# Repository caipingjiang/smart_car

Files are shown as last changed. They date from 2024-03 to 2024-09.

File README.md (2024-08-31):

# 备战日记及感悟
## 十九届智能视觉备战
### 2024/4/10
昨晚偶然间又看了木哥的备战“日记”， 感受很多，颇受启发。感受到有许多值得咱们学习的地方：
- 每个一段时间就反思总结， 回顾近段时间做了什么，明晰下一阶段应该做什么
- 提高效率，有时不要太意气用事，多点理性
- 学习永无止境，热爱就是动力，学习英语即使如此，不必感到烦恼，把它权当你技术学习上的工具，每天坚持
  当然还有许多值得学习借鉴的地方，哈哈，就这么简单写点吧，以后这可以作为我们交流、分享讨论的地方，鼓励大家也来多写写心得体会，bye

### 2024/4/11
目前阶段现状：
1. PCB焊接未搞定(如果板子没问题，尽量在下周结束之前完成-21号)
2. 卡片数据集还有许多类别未拍，可以每天有空就拍一类，轮流拍，完成每日任务任务，不要过于依赖学弟， 导致拍的效率很低？（江老师说得对，压榨学弟不如压榨自己）
3. 车硬件总体调试（尽快要完成了，不能再拖， 周末之前完成）
4. 元素识别稳定性加强，以及在元素部分赛道的运动控制还没完成
5. OpenArt 目标检测以及串口传输数据（如何确保信息的准确性，考虑滤掉一些信息）

故下周主要任务就是4，5，争取让车车先跑起来，模型的准确性先不提
这周拍完数据集，打完标签开始炼丹，不能再拖了

### 2024/4/11
今日工作，像机器人一样拍照，莫得感情，明天继续，拍完四类，难受。
### 2024/4/14
受到木哥指点，认真检查驱动板的焊接，发现普遍存在的虚焊问题，焊了一天板子成功修好以前失败的三块驱动板，焊接技术进阶
数据集拍完，驱动板完成。

### 2024/4/16
下阶段任务 完成二代机械结构，框架加宽，机械臂优化，这次依然使用3d打印，后期优化替换
           探索炼丹技巧
           定下目标检测及分类识别的思路，测试openart可以运行两个模型，但可能是框选不标准导致识别率极低。目标检测重拍，如何拍？
           争取下周之前焊好主板，将车车以前学长的硬件结构替换为自己的，完成硬件任务
           最最最最重要！！！！！！背单词，考四级！

### 2024/5/1
   五一九天假？直接完赛？
   目前阶段现状：主板焊完测试完成，硬件结构以全部替换，机械结构完成，硬件任务完成
                炼丹一直是废丹，继续探索炼丹技巧
                控制代码不断完善，十字运行状态良好，下一步与openart结合进行控制，捡卡片的思路？
                openart分类识别时如何准确的框选出图片？
                调参这种事现阶段还是不要浪费太多时间，还没到死磕的时候目前就是调差不多能用就行吧
       九天的假期相比于之前零碎时间效率还是很高的，这段时间争取完成大部分任务，这段时间也是通宵了两天，（江老师是真的狠人，
     动不动就要调一晚上，相比江老师做的任务量，非常的自愧不如，比起江老师感觉自己有点摆，无比惭愧。注：后面打的都是身体战，如果现在不好好休息，
     后面是绝对撑不住的，江老师保重身体啊！）希望可以利用这次假期完赛吧。（献祭一个江老师）

### 2024/5/2

### 2024/5/3
现在是早上五点，差不多熬了一晚上，现在倒是挺精神的😂，张老师说的没错：后面打的都是身体战！回过头来看看这两三天的调车时光，确实，这就是差距的，一个代码写出来总会遇到各种bug,总是要调试很多次取找出bug所在，每次烧录完程序自信满满地以为这次绝对能行，可最后往往以打脸结束。代码框架先在脑海中初具雏形，到反复调试，找bug, 能运行，考量优化，其实我觉得有很大一部分时间浪费在找bug上。有时觉得自己效率太低，调了半天车，没什么进展，往往内耗自己的情绪；有时做一个事情，半路里觉得“有必要”去先完成另外一件事情，另一件事情做了回儿，觉得另另一件事应该先完成，哈哈，这就是顾此失彼啊，没有把握重点。每天先明晰第一优先级要做的是什么，如果被其他打断，有必要去做那么不是很有必要的事吗？往往是做这做那，就忘了根本的目的。希望以后引以为戒

前段时间张老师也是花了很多时间完成了驱动板和主板的焊接，也算是取得了突破性进展，我要称之为“大交汉武帝”，这几天调车哥们也是一起肝啊，也是辛苦了张老师咧
五一假期已过半，还有几天时光，分析一下下一阶段的工作：
- 练得一手好单，张老师也是练了很多丹了，但效果不是那么令人满意，下一阶段和张老师探讨一下，请教学长
- 该上openart了，先挑卡片矫正，目标检测若效果还行可以加上目标检测看看矫正效果
- 组织一下几个摄像头与核心板的通讯，分析一下总体通讯（小车控制）逻辑
- 数字字母的分类数据集应该也可以拍一拍了，这个效果应该很好
- 可以先拿个MCX Vision玩玩，了解以下怎么使用？

### 2024/5/6
 ！！！！丹成！！！！！
 也是和兄弟们又通宵一天，这次也是有两个学弟的陪伴，学弟的效率也是很高的，一晚上就打完了几千张照片的标签，不知道这算不算压迫学弟😝。
 也是在今天早上终于成神丹，过程也是有点难崩，我可能已经错过了好几次成神丹的机会了，前面无数次效果令人不满意的废丹其实是因为验证错误的问题，
 他们很有可能是神丹的😭，具体原因是逐飞给的分类识别的脚本 img.copy(r.rect()) 的使用错误，它并没有copy出感兴趣区域，而是使用的整个图像，
 这也是在使用目标检测后框出不理想框反而判断更精准而发现，因而出现了种种我们认为不理想的丹，将它改为 img1 = img.copy(1,1, r.rect())  
 就可以了，从中的感悟也是颇深😊。
  放假的这段时间虽然没有完赛但效率也是非常高的，也是和江老师通宵了四五天，现在生物钟都混乱了

- 完成炼丹任务
- 目标检测训练完成，90度分类目标检测良好，虽然可能框的不太准确，但好在丹硬，识别率还是非常高的，130度目标检测效果不太好，会出现近处标不出的问题，后面可能需要重练
- 数字字母的分类识别虽然只练了150多轮，准确率也是高的离谱
- 今天还发现调整openart的亮度也就是曝光时间会影响帧率，在降低曝光时间后帧率提高显著，所以补光灯变成了非常有必要了
- 目前来说任务就只剩和openart结合进行控制了，至于其他的暂且把他们归为优化项（换五分类？换碳板？），目前保证先完赛吧
- 自从调车后也是有点厌学，四级已经一个月没看了😭😭😭，感觉需要找点时间学学四级😔😔

### 2024/5/22
近两周进度推进缓慢，有些停滞
目前mcx已能用于目标检测，部署到实际的行车环境，今晚简单调了下，还有些小问题。
- 弯道可能识别不到卡片，可能是参考点的选择不太合理或者距离计算公式得优化
- 有时会误识别，导致转错方向，why?
- 仓舵机仍是一大问题，时不时还会发癫痫，今晚换了线，明天再试试会不会有问题
- bug:有时转向后会倒着走？
- 主板电源电路的问题，现在先放放？？？？？

下一阶段（6/1之前）：
- 把上面提到的问题，解决
- 把分类加上去，实现与仓配合
- 十字环岛逻辑控制完成
- 放置卡片

加油啊xdm，完成上面的内容也基本完赛了，**提高效率与执行力，不要再拖了**
<u>时间过得很快!!!</u>
<u>时间过得很快!!!</u>
<u>时间过得很快!!!</u>
早日完赛！⛽

### 2024/6/5
!!!!!完赛!!!!!
计划的完赛日期一拖再拖，终于还是完赛了（虽然坡道和障碍还没写😁），完赛情况比预期要好，虽然存在一些问题，但还是比较丝滑。
- 仓抖的问题解决，和预期的一样是因为杜邦线接触不良，也可能是主板硬件的毛病（当时少几类电阻就直接拿差不多阻值的代替了，有点随便😝）在换了线和焊了一块新主板之后就稳得很
- mcx目标检测的问题解决，之前的种种问题完全是因为屏幕太小没有显示整张图像，造成了很多假想的问题，换了块大屏幕之后问题就自然消失了，所以说在调车的时候最忌讳盲调，一定要有人机交互的端口，屏幕或者无线串口。
- openart的卡死问题解决，这个问题也是困扰了我很多天，每天都非常煎熬，以为是内存的问题，因为毕竟运行了三个模型，为此还爆金币又买了一个art(当时舵机也是，一开始以为是坏了，又买了两个舵机，太贵了😭，但是无所谓了，有备着的总是好的，就算是给学弟的积累财富吧，毕竟我们也是传承了木哥当年的车车和大部分元件，希望能传承下去吧），也是今天晚上试车时偶然发现，我们的openart程序中的roi会超出边界，具体原因是因为目标检测框出来的roi会整体偏左，所以在使用roi时进行了手动调整，比如x1 = int((x1-0,1)*img.width())，这时候问题就来了，假如手动调整过后x1,小于零，那么roi显然已经超出了图像范围，所以可以对此加以筛选，if x1<0:  x1=0，就可解决。
- 目前的最急需解决的问题就是放卡片和捡卡片不能一次完成，主要问题是矫正的位置不精确和电磁铁的问题，当然有可能是卡片本身的问题，当时粗制烂造的卡片也是深受其害

-所以下阶段的任务-

- 把避障和坡道的代码写完，坡道可以选择直接不走或加辅助轮冲过去
- 解决放卡片和捡卡片问题，试一试换一个电磁铁，优化一下机械臂路径，优化卡片矫正的算法
- 试车调车，每天都跑一跑车真的有用，每次跑几乎都能发现问题，还有一下隐藏的不容易出现的问题，边试边调一直是我们调车的最佳方案

### 2024/6/5
从前几天开始已经陆续完赛了，昨天又熬了一夜，解决了很多的bug,对控制进行了优化，运行起来丝滑了许多，目前识别和分类的正确率也得到保证了，到目前为止可以说已经基本完赛，若不提完赛用时的话运行起来还算比较稳定，有一定鲁棒性。虽然比预期的完赛日期晚了几天，但也总算完赛了，先庆祝一下🥳🎉

回归之前的问题，这里简单做下总结：
1.卡片的距离计算公式似乎不用太精确，以前以为mcx的前瞻因该很远，故需判断卡片的距离，但目前我们的mcx的前瞻调的较低，画面中只要有卡片，说明就已经不远了，所以这里简单的用像素点之间的距离来代表两者之间的距离，效果也是可以的，所以啊空想不如实际去动手试一下
2.仓舵机的问题之前一直萦绕了我们很久，也换过舵机，买过新舵机，仍然不行，最后发现是**杜邦线接口松动**的问题，只能说"踏破铁鞋无觅处，得来全不费工夫"，现在仓转的很标准，回想之前的转角，一会就差个5度10度，不然就疯狂抖动，现在心情舒畅了
3.转向后倒着走因为识别到了车底盘，同时之前的位置矫正如果坐标不刷新就会一直保持上一状态，导致可能走出赛道，现已改进

下一阶段就是不断测试，不断找潜在的bug,同时进行优化，提高稳定性与完赛速度，目前有以下几点：
0.首先把剩下的坡道和障碍物解决
1.用于分类的目标检测框照片可能还是稍有问题：可以考虑重新框，框得越准自然分类的正确率就会越高
2.加上错误修复，**提高整体的容错性**，比如即使在十字逻辑发生了错乱也不影响在环岛进行操作
3.之前的边界矫正稍微还有点问题，看看能优化进一步提高鲁棒性
4.去掉不必要的延时，在保证卡片识别正确率的基础上加快运行速度，看看能不能到**5min**以内
5.考虑在mcx端对目标直接进行过滤操作，因为有一定概率会误识别停下来，虽然不影响后面的执行，但挺费时间
6.代码优化：尽量把之前的参数声明在全局变量，把相同逻辑封装起来只需改变全局参数即可调参，而不用在相应代码段一个一个一次该让参数好改，易改，一目了然
7.结构优化：补光灯可以加上，仓换新版，框架的强度可以提升，前面支撑摄像头的碳杆得想办法限位，这个最好让他没有活动空间

**说长也长，说短也短，7月份就开始比赛了，6月又有不少考试，一个月过得是真的快，所以啊，后面不能松懈，提高执行力**

### 2024/6/23
最近刚考完电拖和数电，但愿能过吧，也是许久未更新了，搞得都不想更了，想着还是更新记录一下吧
已解决问题：
- 障碍物和坡道基本解决了
- 之前分类之前用于框图片的目标检测框不准的问题是由于，没有将原始图像压缩成正方形，逐飞在群里说明了这个问题
- 代码的容错性提高了一部分呢，但仍有许多可以去提升的
- 边界矫正就是之前y轴设置的目标值的问题，把它目标y值设小一点应该就行了
- 目前去掉了大部分延时，连续拣、放卡片以及模式切换都快了不少
- 加了补光灯，但是接触不良

下一阶段：
- 1 将电磁铁时而吸不起来的问题解决一下，最近调车，这问题太恶心了，C,不知道是线松了还是mos管坏了还有就是补光灯估计是线有点松动，之前仓抖动也是由于线松了，下一步可以全面排查把这类由于线松动接触不良的问题彻底解决
- 2 重调一下边界矫正，之前边界一直都不是很硬，而且目前都是大十字，小十字不知道行不行，此外环岛边界矫正的最大横向速度也是和这个直接挂钩的，争取把它调硬一点（考虑一下把前轮差速给大一点？）
- 3 今天在B站看了一个弯道贼极的赛道，我在想会不会误判，由此想到可以把之前的环岛/十字/障碍物检测优化一下，加强鲁棒性
- 4 还有就是检测三大类放置区，虽然目前感觉没啥问题，但我感觉还得优化，之前写的感觉太就简单了，而且也是可以将
- 5 之前的一个bug: 不知道是检测到了其他杂物还是其它什么原因，小车在转弯完成后会慢慢的移动，想不明白，之前我是针对这个问题改过的，在postion_correct里特意加了如果串口1没有识别道卡片（或者卡片距离没有小于目标值）就给小车速度赋值为0，但是现在它却在慢慢移动?是很缓慢的那种移动，？？？
- 6 接上一条，我感觉不一定是矫正这一部分出问题，在矫正之后可能也有问题，回头将这部分时序再排查一下
- 7 mcx目标检测目前对于字母“I”很容易识别不到，稍微换下角度就行了？要不要重新打标签，或者把mcx安装位置后移
- 8 目前测试的卡片就那固定的几类，后面换成其他没有测试过的类别再测测
- 9 对于有部分卡片识别结果会在几个字母之间跳变，这种是丹的问题吗？如果实在不能解决，可以写一下判断，直接放弃这张卡片，不至于一直卡在这
- 10 最后就是多跑，多测试了，后面可能反而能跑的时间不如现在多，趁现在多跑跑找bug吧

### 2024/7/7

！！！灵感爆发，突破性进展！！！
  今天也是又和兄弟们熬了一夜，果然晚上才是灵感爆发的时候，之前一直苦于有时候捡一次卡片捡不起来或者不小心没放下而需要捡第二次，但对于环岛和十字这种对卡片次序要求非常高的卡片堆无疑是巨大的灾难，几乎是只要是一次捡不起来多捡一次或者交换仓中卡片或放卡片出错后面的都会错，几乎每次跑一圈都会有这种问题，非常恶心人，从调车开始恶心到现在，之前一直考虑提高电磁铁和机械臂的角度，但问题没有得到很好的解决，如何知道有没有成功捡起或放下卡片也一直没有很好的解决方案，因为目前的结构确实没有可以检测的东西，但为什么不加一个呢？于是顺着这个想法感受到了极高的可行性，不就是加一个接近检测或者测距模块吗，于是我们采用了用于循迹小车的红外对射管，随便找了个之后测试非常可行遂熬夜一天给车车加了一块，调试后也是非常顺人心意，这一个小小的改动为我们解决了一个非常致命的问题，也不知道为什么以前没想到😞，今晚加油调，我有预感今晚会完美完赛😍😍😍
  
-电测铁有很大一部分原因是线虚的问题，刚才也是发现它断了，当然也有角度的问题，但随着我们可以知道是否捡到卡片，我们就可以知道卡片的数目而去自动调整角度，还可以无限次数的捡和放而不对记录的卡片次序产生影响，这个问题以后会得到很好的解决。
- 小车在转弯完成后会慢慢的移动的原因是当时写代码的逻辑问题，现在已经解决。

- 现在bug还是很多，但好在我们现在可以知道是否捡到卡片，大部分bug会得到解决。
- 将是否捡到卡片的判断加到捡和放卡片的逻辑中，包括捡卡片，放卡片和交换
- 试一试红外对射管的稳定性，据说会受日光影响
- 需要自己制作红外对射管，补光灯和转接板，并在铜层加队伍信息
- 弯道和s弯的卡片有时候会转错放下或者看不到
- 最后就是多跑，多测试了，时间剩的并不是很多，尤其是现在期末周有很多考试（明天考电机学，大后天考复变，还没复习呢😭😭😭），继续找bug解决bug。   加油！！！

-
今天早上也是试了试，光照对光电传感器影响还是挺大的，又是思考了半天如何解决这个问题，然后突然灵光乍现，为什么非要用电子传感器去完成这个功能呢，一个小小的微动开关也可以做到，而且抗干扰能力直接拉满😎😎😎😎

### 2024/7/27
现在是中午12点半，坐在回程的动车上，望着窗外一片青翠的景色，一动不动发了会呆，哈哈感叹恍然间省赛就这么结束了
感谢！省赛没出太大意外，还碰巧让我们拿了第一😁

回想两周前，从刚考完最后一门考试，感叹着时间紧，任务重，车的稳定性非常有待提高……感觉有些许焦虑，再到后面扣细节，把没有必要的延时去掉或缩短，把车车的转向过程优化，把各种能提高鲁棒性的判断加入，把新遇到的bug及时解决，虽通宵调车，却也收获颇丰。
21日，多亏了焦老师我们得以去大连民族大学测试车车的稳定性。不得不说去了现场发现他们实验室比我们实验室亮了很多，当时第一感觉是亮度对巡线和识别的影像应该不是不是那么大，然而当我给车模上电，把车车放在赛道上时，才发现mcx过曝非常严重，屏幕显示中心部分严重白化，对目标检测影响非常大。总钻风也因亮度的原因，巡线出了问题，斑马线也因此没识别到。说实话当时还是比较慌的，因为我在模拟这就是到时候真正比赛的赛道，如果到时候我们也遇到这问题能冷静应对吗。可能是我们从一开始就一直在自己的实验室调试，没有去其它场地调试过，因此一直以来我们的曝光度都没怎么改过。也正是这个原因，我们在当时没有第一时间反应过来去改曝光度。好在后面我们开了屏幕，又把总装风采集到的灰度值显示在屏幕上面，才发现了问题所在。后面在改了曝光时间后，我们在他们场地跑了几圈，感觉问题不是很大，于是下午就回去了。

回去已经将近晚上9点了，学校已关门，因此我们只能抱着车车回到租房的地方睡了一晚。第二天到了22号，也就是我们正式出发前的最后一天。早上起来9点多了，没办法，再把车车抱回实验室，开调！调到下午那会发现仓的转动出了问题，在交换卡片时，会由于仓转动角度不准，导致电磁铁吸附时端面没有与卡片平齐而吸不起来，以为舵机坏了，拆仓、代码调偏移角度。最后都感觉不是这些原因，后面把仓下面的线压平一点，似乎问题解决了，怀疑是下面的线和上面的仓之间的摩擦力太大了，导致最后仓不能转到指定角度；之前写了一个防止误捡字母卡片的判断，但是就很离谱：冲环岛一侧测试没问题，但从另一侧测试发现始终有问题，后来发现把速度降低就行了；后面强化训练环岛和十字部分，发现有一定概率，会把识别到的字母给晃掉。于是加了个蜂鸣器，才发现原来在反复进行判断，根本没有进入后面的循环，后面经过改正后，环岛十字的稳定性得到了极大提升。也可能正是由于改了这个，在后面art识别时，出现了一点问题，有些识别错误。后面想，应该是没有延时进行缓冲，于是在后面的判断中先加上延时1s在进行判断，就没有问题了！自此我感觉我们的车车稳定性应该是比较好的了，至少要比之前好不少。唯一遗憾的是在转向完成时会有停顿一会，没有之前的丝滑了，就很玄学，在去大连民族之前完全没有出现过这个问题，不过也还好，除了看着很难受，浪费了十多秒，对总体感觉影响不大。到这已是次日的4点，心想还可以再睡4个小时

24日，到了长春，上交车模。抽签比赛顺序，最后抽到了第二个上场。既是不幸也是万幸。不幸的是比赛顺序太靠前，可能没有太多准备与调试时间；万幸的是，当时我们第二个上场，由于裁判放卡片不小心放多了，之前计时时间不算，重新清零20分钟，相当于在初赛解了我们的燃眉之急。纵观初赛与决赛，发现大多数队伍在调试的时间上占用太长了：本来总共20分钟的比赛用时，可能调试都花了5～10分钟，我们队还好，在初赛把曝光度给调好之后，决赛上场前以及上场比赛时几乎没再调过参数，直接上场就发车，这里也得感谢赛前的大连民族之旅，给我们打了一剂强心针。这里额外提一下：我们的总装风会根据采集到的图像计算出参考的白色灰度值，但之前我们进行了优化，并不是完全根据采集是灰度计算白色参考灰度值，而是有一个基础白色灰度值（我记得应该是130），而且基础灰度值的占比为0.7，采集得来的灰度值占比为0.3。之前这样优化是为了避免采集图像拍摄的区域不在赛道上或者赛道上有部分黑影而影响整体计算出的白色参考灰度值。但这样做的弊端就是，没到一个新的场地，得重新调节一下曝光时间，使起采集得来的灰度值就在130左右。这样就相当于在基础灰度值的基础上加上一个全局动态灰度值，这样即可以考虑到同一赛道不同地方由于灯光影响导致的亮度不一样，也可以避免采集图像有问题而导致最终计算出的白色灰度值偏差的太离谱省赛就这样告一段落了，还有许多想要说的，这里就不一一列举了...

这里得感谢木哥旺哥博哥，在我们最后的备赛期间为申请实验室而四处联系，感谢一起调车时焦老师和张老师的陪伴，感谢山哥的帮助，感谢徐老师的精神陪伴与鼓励，感觉王老师的带队工作，感谢学社，感谢陈老师，感谢所有的兄弟们，咱们哈尔滨再见！

张老师和江老师辛苦😭，望诸位兄弟都能所得即所愿，哈尔滨书写新篇！

### 2024/8/23

  哈尔滨之旅圆满结束！！！一切都像做梦一样，这次也是拿到了梦寐以求的国一和凤凰佬的签名和合照，最最最最重要的是也又一次见到了徐老师😍。

  自省赛结束这段时间也是比较懈怠，也没多在智能车上浪费时间，回去之后马上就和江老师开始了电赛的任务，从出题开始四天三夜
也是比较抽象，前两天都在搭结构大螺丝，直到最后一天才稍微有点起色，连夜写完了大部分控制代码，也是非常极限，电赛从做到交作品演示大概花了五六天的时间，只能说非常折磨人，今年又是省赛年也不好玩，最后省二而归。整完就和江老师商量了车车的结构问题，因为各种原因，结构也没有大改，基本采用以前的结构，多加了几个补光灯，换了个大的电磁铁，但最后好像用处不是很大，赛场上的灯光太强，影子依然是有，观看其他学校的结构，我感觉我们的机械表似乎有点太结实，相比于那些晃晃的机械臂，这样反而不好，角度有一点不对就会吸不上来，这个问题也是从调车开始就一直恶心我们到现在，然后就是把仓下面挡住防止下面的线摩擦到仓。也有过想换五分类仓，但一是经费不足，二是又很浪费时间也快不了多少，要是加仓门的话主板又要改，最后就没有变动。改完结构的后面这段时间我也是没有怎么调车，和江老师这段时间也是比较轻松，比较懈怠。后面基本上都是江老师断断续续的调，我也是好久没看代码，从这里反省一下😁。

  我其实一直以来是比较求稳的，在车车没稳定之前我是不会去想让它去提升，省赛之后虽然跑的非常好，但感觉还是有很多问题，江老师一直都在追求速度，中间也是有很多意见的不同。不知道为什么，感觉不管是电赛还是智能车还是电赛，我们都做的很极限，智能车省赛，电赛都是比赛前一天才调好，这次依然一样😂，17号晚上，也就是要出发前的前一天，我们才开始让车车跑全场，最后当然是非常不好，这里再次反思一下，不该这么懈怠。然后就开始连夜调车，调的过程中又发现仓又转不准，然后就是拆了又装，装了又拆，幸好最后发现只是舵盘的螺丝没拧紧，然后就继续调车，接着就是各种奇怪的问题，舵机烧了连夜换舵机，又是拆了木哥去年的仓（这次木哥的国赛车车真的被我们完全拆干净了🥺），运动姿态不对，捡不上来，反正就是完赛不了，甚至我已经换上了省赛的代码，一直调，调到了第二天下午，最后才勉强完赛，这时候已经差不多都是省赛代码了，已经做好了国二万岁的准备匆匆出发。

  来到比赛的前一天，有一次调车的时间，一个队20分钟，我们和电子科技大学合起来拿到了40分钟的调车时间，调试的时候也是出了很多问题，光是起跑线的曝光度就调了十几分钟，最后跑整圈的时候还出现了因为仓里的卡片太多所以放的时候发不下的问题，结束后心情也是既忐忑又紧张，再酒店又调了一会，和江老师商量了下对策，决定先环岛十字都关保证完赛，后面再上优化的版本。有因为种种原因，视觉组改为只有一次比赛，不进行预赛决赛制，到了比赛的那天也是非常紧张，幸运的是，上场前车车得到了徐老师和旺哥的虔诚跪拜，上场比赛的时候一切都非常顺利，保证完赛的版本一遍就过，保证了国二，后来又上了快速的版本，也是一遍过，这里也多亏了江老师调的快速版本，不然真不一定能国一😘……

  回去路上徐老师让我们注意来时的风景和现在的风景，感觉一切都不一样了，轻松，欢快，对付出得到回报的欣慰，一切都是对这一学期艰难的最好慰藉。

  最后一定要感谢一下徐老师木哥对学弟的传承与教授，旺哥博哥为我们申请实验室的奔波和他们的陪伴（感谢旺哥送黑神话悟空，让我直面天命😍😍😍），学长们的陪伴与关心让我感受到了家的温暖，感谢焦老师江老师亦师亦友，感谢青哥和山哥的陪伴与帮助，在华发新城和兄弟们生活的这段日子难以忘怀，我也得到了很大的提升。感谢冯忠英师兄和李婷婷师姐的热情款待，真的没想到远在哈尔滨还有电子学社的家人款待陪伴我们，感谢陈老师，感谢电子学社。希望以后的学弟学妹们继续探索，再创新辉煌。

  虽然但是四级好像又挂了😊😊😊😊😊😊

### 2024/8/24
国赛结束，拿下国一🎉🎉🎉

省赛回来后，刚开始有想改五分类的想法，也想过借鉴他们的储物仓，要不要升级成可一次性卸卡片的储物仓，但后面碍于打印机坏了的窘境以及想摆烂的想法，于是最终决定就沿用之前的四分类，转为优化一些运行速度以及提高控制的稳定性

其实从一开始，我们的想法就是直接用一个四分类，让车壳的体积尽量小。卡片无非就分为散落卡片（最多3类）和圆环卡片（最多5类），因此仓的数量根据圆环最多卡片类别5类设置即可，可以说5分类是比较合理的的选择。四分类在圆环元素分拣卡片遇到有5类卡片时，我们选择把第五类重叠在第一类上，因此在放置卡片时我们有时会把其中一个仓的卡片先移到另一个仓，再将下面的卡片放置出去。

前段时间把实验室里不知道哪届学长的圣遗物一张弓拿来玩了玩，调车调累了就去实验室的另一头射射箭，哈哈。由于省赛之后几乎没怎么改结构，所以在调试时基本就是在原来的地方改了改，优化了一下，期间感觉比较枯燥，因此在去哈尔滨的前几天，我白天一半时间在调车，一半时间在射箭，难崩，可能正是这个原因后面来了报应😂。

先简单说说这期间优化的几点：1. 将车身转向与机械臂拾取卡片这两个同时进行，尽可能缩短了拾取时间。2. 微调了一下循迹的pid，让目标检测的视野更贴近在赛道中央，这样可以避免在一些s弯道因视野盲区而漏检卡片。3.加上了多级菜单调参，以备国赛决赛时不让下载代码的情形。4. 将各种不必要的延时，以及不必要的时间浪费进行优化，在保证基本稳定的情况下，去掉不合理的操作

说来你可能不信，出发前的几小时我还在调车，哈哈只怪自己太憨了。出发前的最后一天，本想着调一下循迹的pid参数，调了一半，由于是共用赛道，模型组的焦老师准备调会儿。也罢，我便出来去实验另一边射箭。很久之后，玩累了，见见焦老师电池充电去了，那好，我也去调调吧。一调一个不对劲，后面发现小车循迹时很晃动，一开始以为是总装风的问题，因为之前发现总转风初始化的时候，在同一个位置，每次初始化得到的平均灰度值都会差很大。后面复位了几次，仍然不行，很是懊恼，又是加上屏幕显示灰度值，又是查看图像处理的边线，感觉都没问题。十分懊恼。调到后半夜，祸不单行，机械臂小臂的舵机坏了，不能复位，只好再一次打螺丝，更换了新的舵机。又开始重新调了机械臂的角度，都快出发了，还更换机械谁能懂。又是一个通宵调车，越调越烂，累，身心俱疲。后面想了一下，要完赛都完赛不了那我调鸡毛啊。把之前的代码烧进去试了试，似乎比目前的版本好了些。于是乎，对照了之前的代码才发现之前随便的改的循迹pid参数没有复位，kd本是15，之前改成1.5试试效果，后面去射箭，忘改回来了，joker🤡！ 改完之后，感觉还行，想着先跑一圈完赛看看，后面发现放三大类时又有了问题：放完一个位置时，后面的两类，车车大概率不识别直接走了，离谱。这种问题，之前可从没有过，后面试了多次，也检查了多次，也是没找出问题所在。后面张老师把openart识别的脚本改了回去，似乎放置又可以了。这期间由于各种问题的集中出现，我把之前比较快的版本几乎又改回省赛时的了。这时感叹，半个多月改了个寂寞，唉！不甘心，那又怎样呢，先保证完赛吧，保住之前的成果。下午6点多的火车，准备4点多出发，最后我也几乎调到了3点，最后回去洗了个澡，怀着忐忑的心情就这样出发了。这倒是和省赛前的最后一天挺像，哈哈，每次赛前都得搞一波心态

到了哈尔滨，找到了宾馆，赛事方安排第一天进行调试，在曝光上调了调，斑马线环岛十字这些都测了测，最后在放三大类的时候有一类由于卡片实在太多，电磁铁无法与卡片贴合，导致放不出卡片，不过还好，这个卡片时是我们当时随便放的，比赛时某一类肯定不会放这么多。第二天，由于群友们的各种争论，卓大决定视觉组只有一次决赛，没有预赛，由于我们靠后，比赛时间安排在了后一天。当天晚上想了下对策，先把环岛十字注释掉，跑一个有效成绩，然后想了想又把之前快的那一版改到了目前版本里，同时又备份了改之前的最后一版。这样就相当于有了三个版本。第二天一早六点半就起来了，抱着车车到了哈工程，8点多开测，很顺利，一次发车有了成绩，国二有了，于是乎第二次就赌了一把，直接用了前一晚在酒店改的代码，也很顺利，也完赛了，不过有两个卡片识别出了问题，罚时60s，最终成绩300s出头，后面接着又发了几次车，不过最终成绩都在300s左右，就这样比赛顺利结束。感谢徐老师在赛前为我们车车虔诚地磕了几个头，我哭死😭。国赛也算是有惊无险，拿下国一。

赛后，冯学长和李师姐分别请我们吃了两顿大餐，我们接着去了中央大街，去了江边...wan玩的很开心。比较遗憾的是未能求得卓大的签名与合照，不过这也无伤大雅。第二天，我们坐着卧铺回到了大连，归程很是感慨，尽在不言中

致谢：非常感谢冯学长和李师姐的热情招待，让我们品味了哈尔滨的美食，心情很舒畅😄。大二的智能车生涯也算是圆满结束了。非常感谢徐老师的到来，非常感动，徐老师还能来到国赛现场，陪伴我们，感谢遇见徐老师，留下了很多珍贵的回忆；再一次向旺哥，木哥，博哥表示感谢，前期为我们暑假申请实验室做了很多工作，幸苦哥们了；感谢张老师、焦老师在一起调车时的陪伴；感谢山哥和青青的帮助；感谢所遇到智能车友们；感谢电子学社这个大家庭，感谢陈老师；感谢智能车竞赛，让我一路上学会了很多东西；感谢一直陪伴我们的车车，辛苦了😁

前方的路还很远，我们仍将秉持智能车披荆斩棘的精神继续前行，臻图不止，征途不止。祝各位车友都能得其所愿，再见

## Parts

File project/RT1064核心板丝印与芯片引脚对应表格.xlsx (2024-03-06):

GPIO编号 | PAD名称
RT1064 没有端口A
B0 | GPIO_AD_B0_00
B1 | GPIO_AD_B0_01
B2 | GPIO_AD_B0_02
B3 | GPIO_AD_B0_03
B4 | GPIO_AD_B0_04 | 核心板未引出
B5 | GPIO_AD_B0_05 | 核心板未引出
B6 | GPIO_AD_B0_06 | 核心板未引出
B7 | GPIO_AD_B0_07 | 核心板未引出
B8 | GPIO_AD_B0_08 | 核心板未引出
B9 | GPIO_AD_B0_09
B10 | GPIO_AD_B0_10
B11 | GPIO_AD_B0_11
B12 | GPIO_AD_B0_12
B13 | GPIO_AD_B0_13
B14 | GPIO_AD_B0_14
B15 | GPIO_AD_B0_15
B16 | GPIO_AD_B1_00
B17 | GPIO_AD_B1_01
B18 | GPIO_AD_B1_02
B19 | GPIO_AD_B1_03
B20 | GPIO_AD_B1_04
B21 | GPIO_AD_B1_05
B22 | GPIO_AD_B1_06
B23 | GPIO_AD_B1_07
B24 | GPIO_AD_B1_08
B25 | GPIO_AD_B1_09
B26 | GPIO_AD_B1_10
B27 | GPIO_AD_B1_11
B28 | GPIO_AD_B1_12
B29 | GPIO_AD_B1_13
B30 | GPIO_AD_B1_14
B31 | GPIO_AD_B1_15
C0 | GPIO_B0_00
C1 | GPIO_B0_01
C2 | GPIO_B0_02
C3 | GPIO_B0_03
C4 | GPIO_B0_04
C5 | GPIO_B0_05
C6 | GPIO_B0_06
C7 | GPIO_B0_07
C8 | GPIO_B0_08
C9 | GPIO_B0_09
C10 | GPIO_B0_10
C11 | GPIO_B0_11
C12 | GPIO_B0_12
C13 | GPIO_B0_13
C14 | GPIO_B0_14
C15 | GPIO_B0_15
C16 | GPIO_B1_00
C17 | GPIO_B1_01
C18 | GPIO_B1_02
C19 | GPIO_B1_03
C20 | GPIO_B1_04
C21 | GPIO_B1_05
C22 | GPIO_B1_06
C23 | GPIO_B1_07
C24 | GPIO_B1_08
C25 | GPIO_B1_09
C26 | GPIO_B1_10
C27 | GPIO_B1_11
C28 | GPIO_B1_12
C29 | GPIO_B1_13
C30 | GPIO_B1_14
C31 | GPIO_B1_15
D0 | GPIO_SD_B1_00
D1 | GPIO_SD_B1_01
D2 | GPIO_SD_B1_02
D3 | GPIO_SD_B1_03
D4 | GPIO_SD_B1_04
D5 | GPIO_SD_B1_05 | 核心板未引出
D6 | GPIO_SD_B1_06 | 核心板未引出
D7 | GPIO_SD_B1_07 | 核心板未引出
D8 | GPIO_SD_B1_08 | 核心板未引出
D9 | GPIO_SD_B1_09 | 核心板未引出
D10 | GPIO_SD_B1_10 | 核心板未引出
D11 | GPIO_SD_B1_11 | 核心板未引出
D12 | GPIO_SD_B0_00
D13 | GPIO_SD_B0_01
D14 | GPIO_SD_B0_02
D15 | GPIO_SD_B0_03
D16 | GPIO_SD_B0_04
D17 | GPIO_SD_B0_05
D18 | GPIO_EMC_32 | 核心板未引出
D19 | GPIO_EMC_33 | 核心板未引出
D20 | GPIO_EMC_34 | 核心板未引出
D21 | GPIO_EMC_35 | 核心板未引出
D22 | GPIO_EMC_36 | 核心板未引出
D23 | GPIO_EMC_37 | 核心板未引出
D24 | GPIO_EMC_38 | 核心板未引出
D25 | GPIO_EMC_39 | 核心板未引出
D26 | GPIO_EMC_40
D27 | GPIO_EMC_41
D28 | 无此引脚
D29 | 无此引脚
D30 | 无此引脚
D31 | 无此引脚
E0 | GPIO_EMC_00 | E端口被SDRAM占用因此全部未引出
E1 | GPIO_EMC_01 | E端口被SDRAM占用因此全部未引出
E2 | GPIO_EMC_02 | E端口被SDRAM占用因此全部未引出
E3 | GPIO_EMC_03 | E端口被SDRAM占用因此全部未引出
E4 | GPIO_EMC_04 | E端口被SDRAM占用因此全部未引出
E5 | GPIO_EMC_05 | E端口被SDRAM占用因此全部未引出
E6 | GPIO_EMC_06 | E端口被SDRAM占用因此全部未引出
E7 | GPIO_EMC_07 | E端口被SDRAM占用因此全部未引出
E8 | GPIO_EMC_08 | E端口被SDRAM占用因此全部未引出
E9 | GPIO_EMC_09 | E端口被SDRAM占用因此全部未引出
E10 | GPIO_EMC_10 | E端口被SDRAM占用因此全部未引出
E11 | GPIO_EMC_11 | E端口被SDRAM占用因此全部未引出
E12 | GPIO_EMC_12 | E端口被SDRAM占用因此全部未引出
E13 | GPIO_EMC_13 | E端口被SDRAM占用因此全部未引出
E14 | GPIO_EMC_14 | E端口被SDRAM占用因此全部未引出
E15 | GPIO_EMC_15 | E端口被SDRAM占用因此全部未引出
E16 | GPIO_EMC_16 | E端口被SDRAM占用因此全部未引出
E17 | GPIO_EMC_17 | E端口被SDRAM占用因此全部未引出
E18 | GPIO_EMC_18 | E端口被SDRAM占用因此全部未引出
E19 | GPIO_EMC_19 | E端口被SDRAM占用因此全部未引出
E20 | GPIO_EMC_20 | E端口被SDRAM占用因此全部未引出
E21 | GPIO_EMC_21 | E端口被SDRAM占用因此全部未引出
E22 | GPIO_EMC_22 | E端口被SDRAM占用因此全部未引出
E23 | GPIO_EMC_23 | E端口被SDRAM占用因此全部未引出
E24 | GPIO_EMC_24 | E端口被SDRAM占用因此全部未引出
E25 | GPIO_EMC_25 | E端口被SDRAM占用因此全部未引出
E26 | GPIO_EMC_26 | E端口被SDRAM占用因此全部未引出
E27 | GPIO_EMC_27 | E端口被SDRAM占用因此全部未引出
E28 | GPIO_EMC_28 | E端口被SDRAM占用因此全部未引出
E29 | GPIO_EMC_29 | E端口被SDRAM占用因此全部未引出
E30 | GPIO_EMC_30 | E端口被SDRAM占用因此全部未引出
E31 | GPIO_EMC_31 | E端口被SDRAM占用因此全部未引出
F0 | SNVS_WAKEUP | 特殊引脚核心板未引出
F1 | SNVS_PMIC_ON_REQ | 特殊引脚核心板未引出
F2 | SNVS_PMIC_STBY_REQ | 特殊引脚核心板未引出

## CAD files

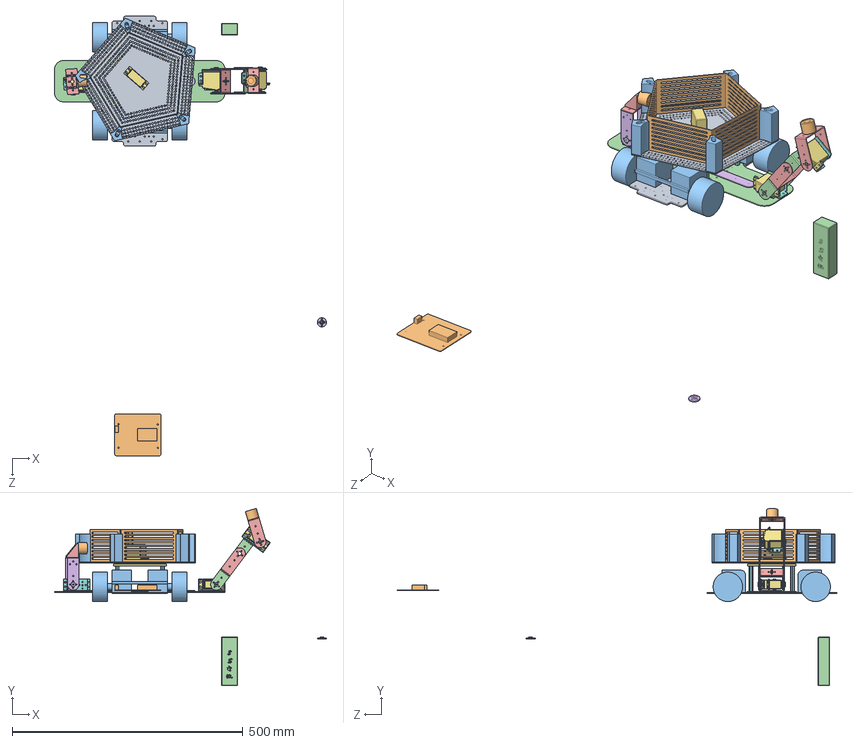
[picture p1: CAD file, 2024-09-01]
model/智能视觉车四分类/五分类/装配体2.SLDASM
589.8 x 384.3 x 953.2 mm
M车底盘
电路板底板
电机替代 x 2
短U支架 x 2
长U支架 x 2
舵盘 x 4
舵机1 x 4
万能支架 x 3
杯式轴承 x 3
电磁铁 x 2
推力轴承
零件3
电磁铁支架
固定
仓支架
铜柱 x 4
零件1
仓挡板 x 5
仓零件 x 5
电池
左舵机支架
左舵机支架1 x 2

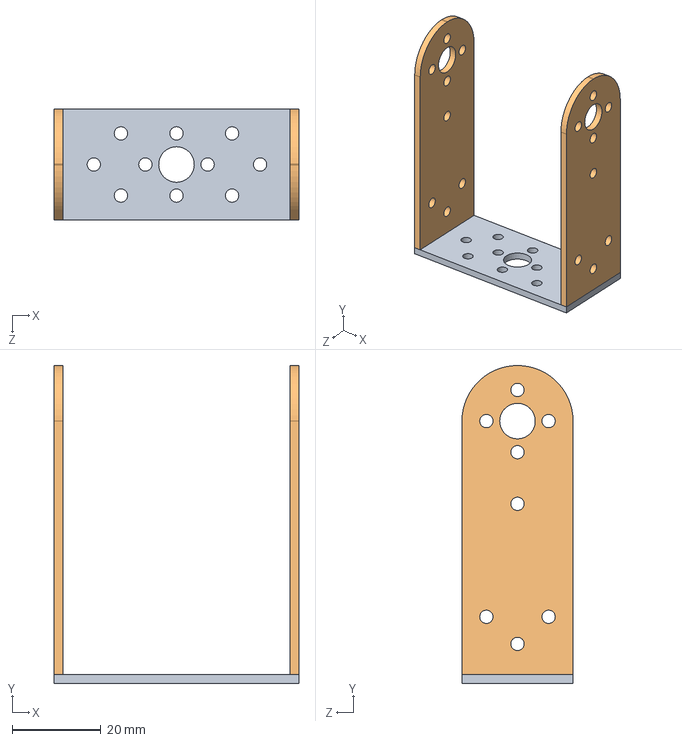
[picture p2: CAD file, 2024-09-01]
model/智能视觉车四分类/五分类/左舵机支架.SLDASM
55.0 x 71.5 x 25.0 mm
左舵机支架
左舵机支架1 x 2

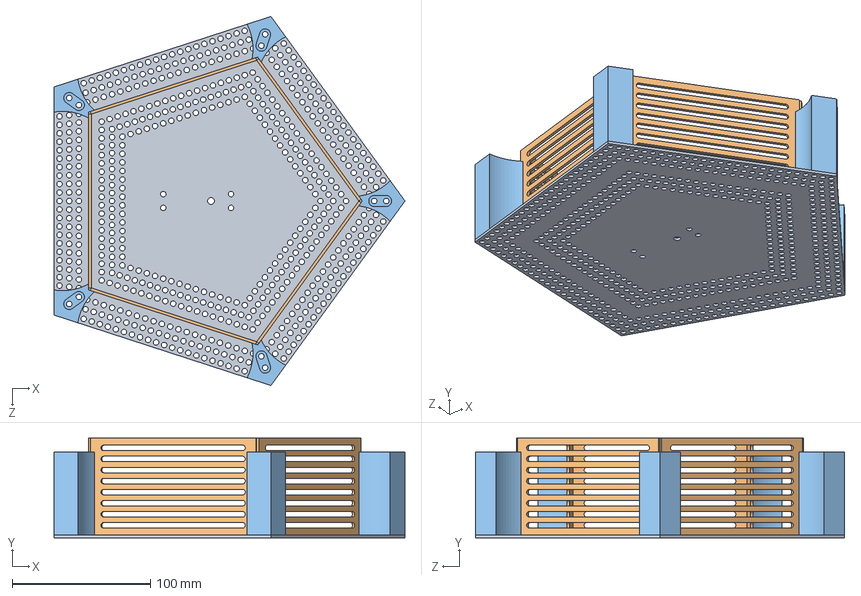
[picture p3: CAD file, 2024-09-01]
model/智能视觉车四分类/五分类/仓2.SLDASM
253.9 x 72.0 x 267.0 mm
零件1
仓挡板 x 5
仓零件 x 5

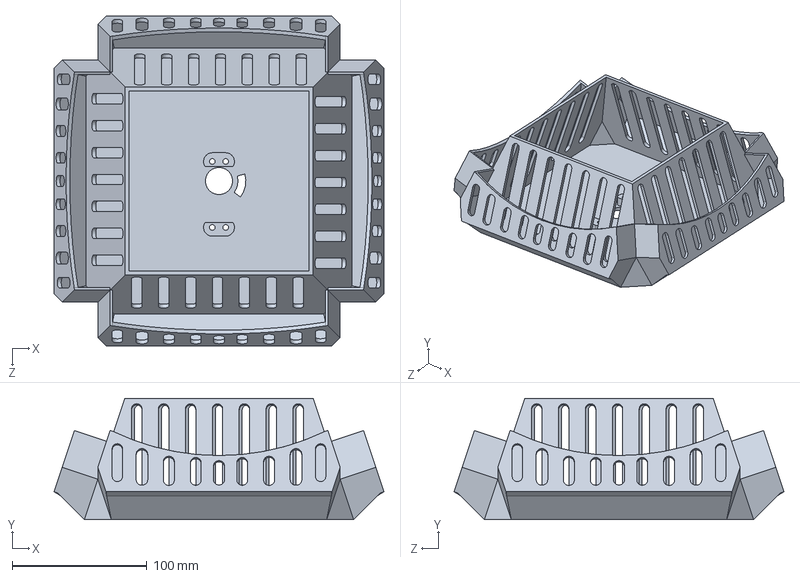
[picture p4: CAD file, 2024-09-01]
model/四分类/仓2.SLDPRT
245.2 x 90.0 x 245.2 mm

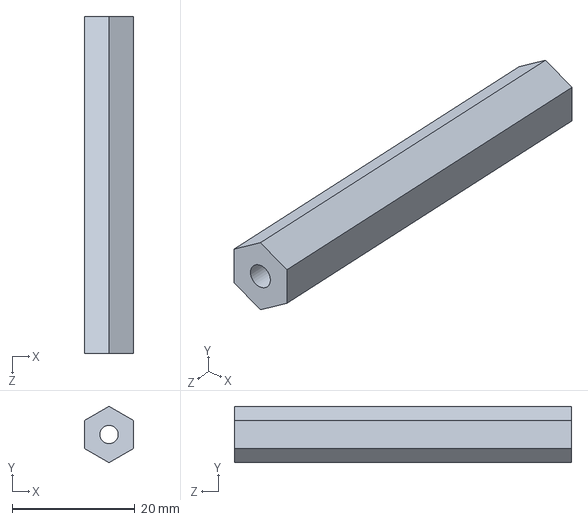
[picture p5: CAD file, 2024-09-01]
model/智能视觉车四分类/五分类/铜柱.SLDPRT
7.97 x 9.20 x 55.0 mm

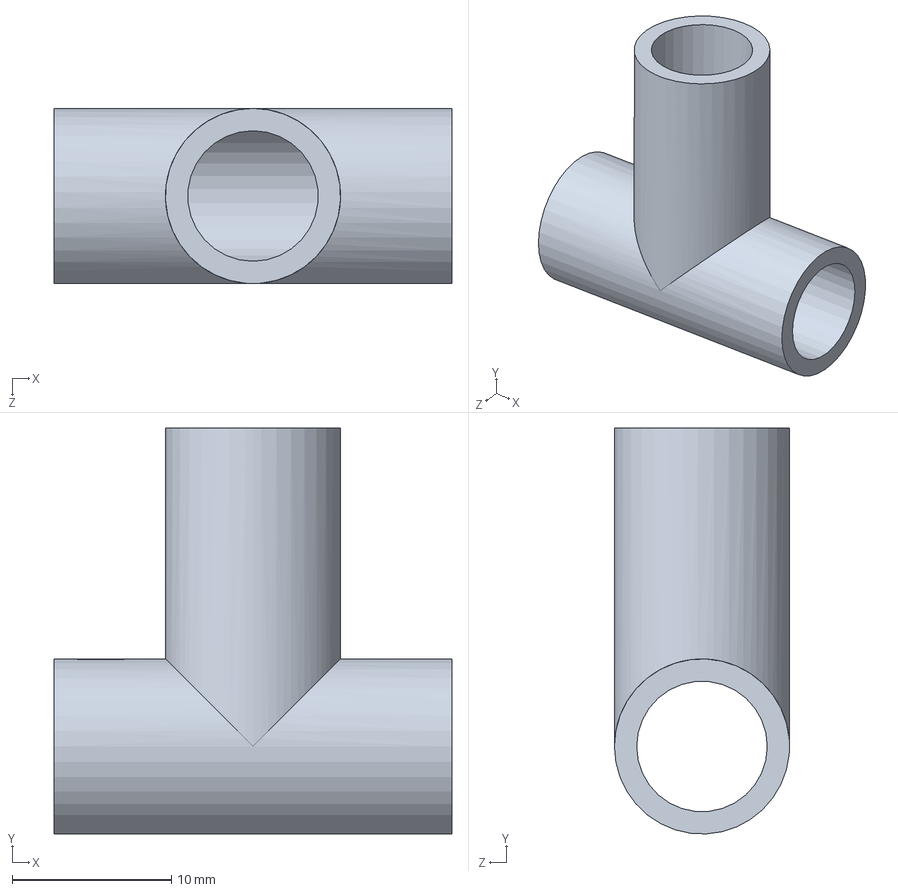
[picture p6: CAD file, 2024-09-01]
model/智能视觉车四分类/四分类/三通2.SLDPRT
25.0 x 25.5 x 11.0 mm

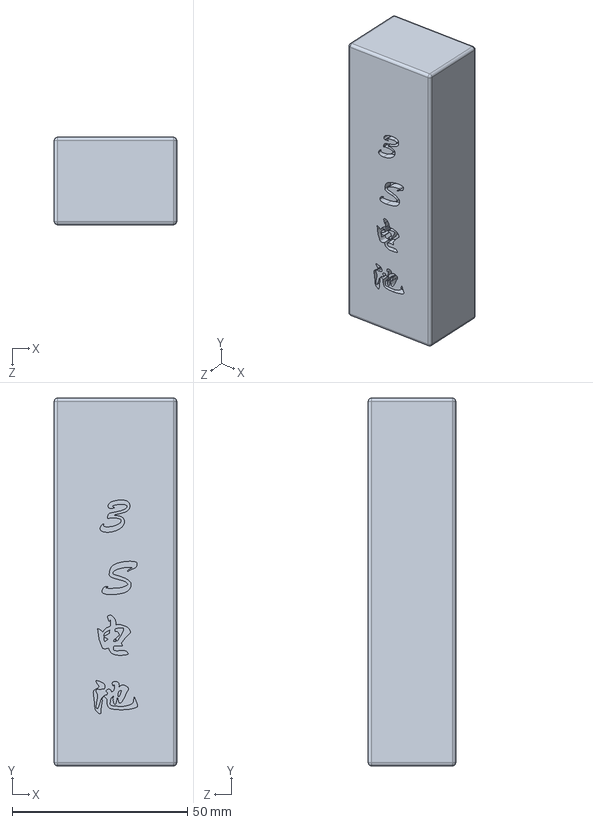
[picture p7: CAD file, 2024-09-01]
model/智能视觉车四分类/电池.SLDPRT
35.0 x 105.0 x 25.0 mm

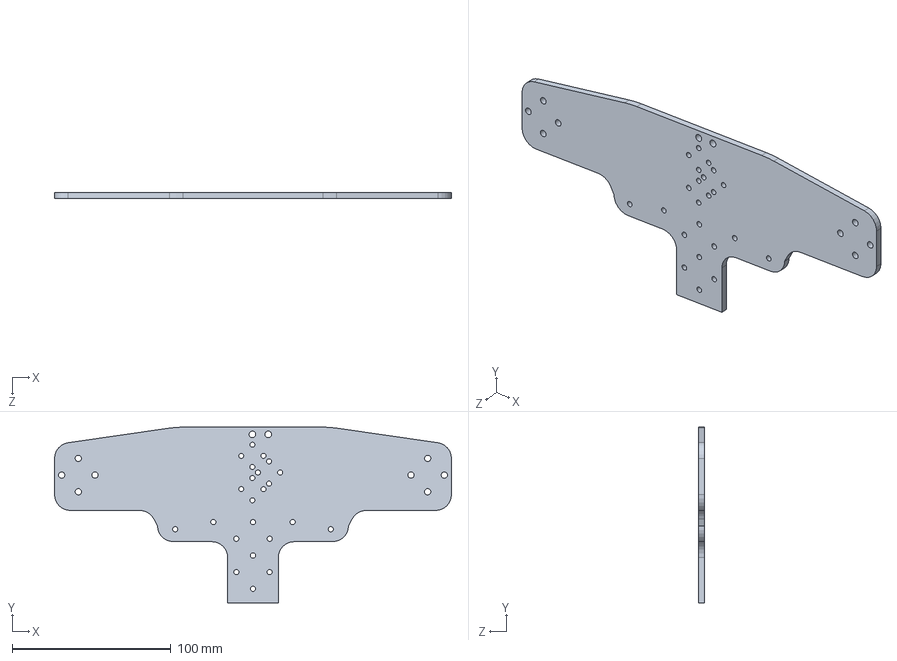
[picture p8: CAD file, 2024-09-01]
model/五分类/前支撑小.SLDPRT
250.0 x 110.7 x 4.00 mm

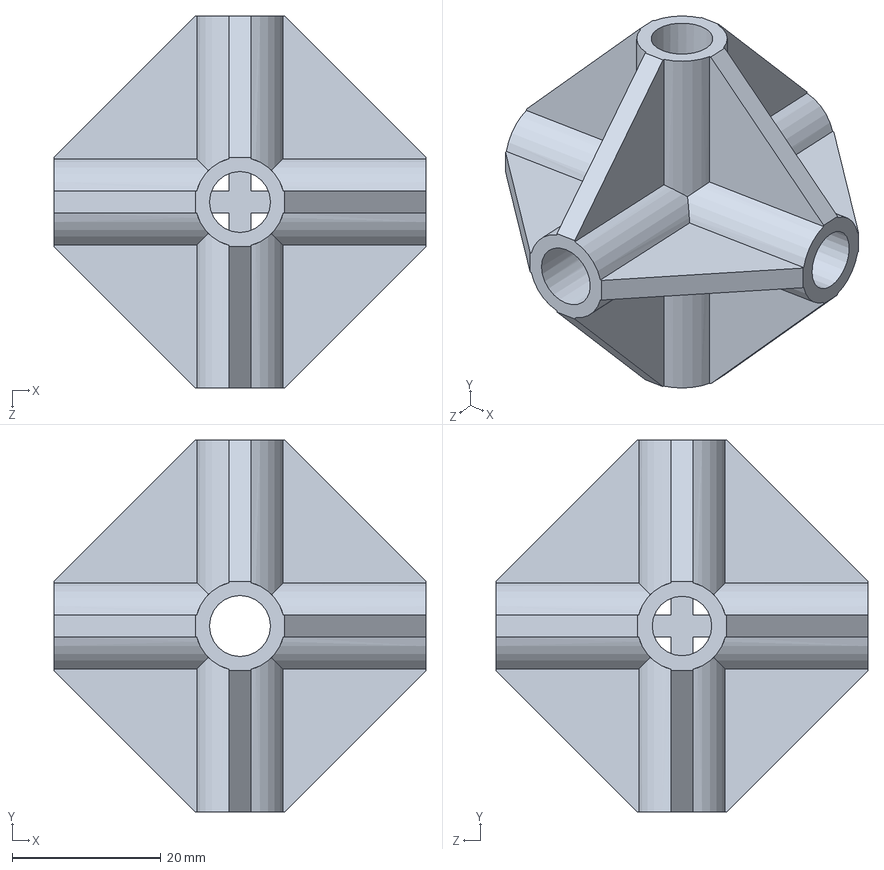
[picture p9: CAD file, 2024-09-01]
model/四分类/十字通.SLDPRT
50.0 x 50.0 x 50.0 mm

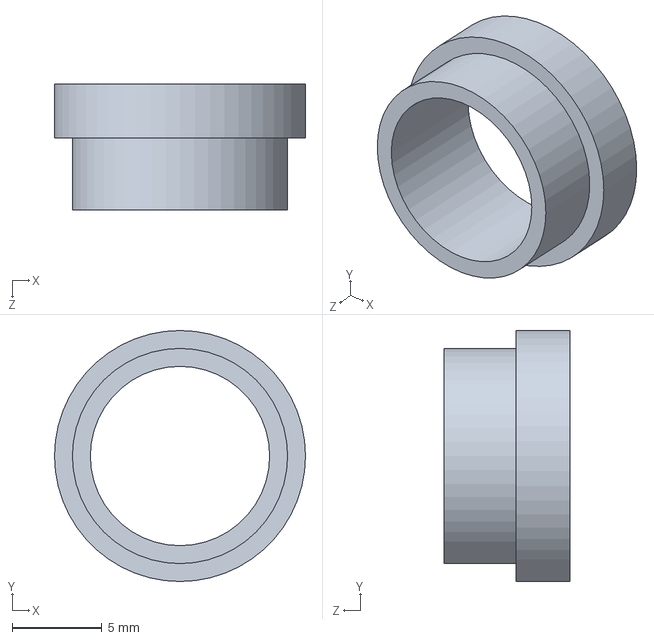
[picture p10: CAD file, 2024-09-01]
model/智能视觉车四分类/四分类/镜头套.SLDPRT
14.0 x 14.0 x 7.00 mm

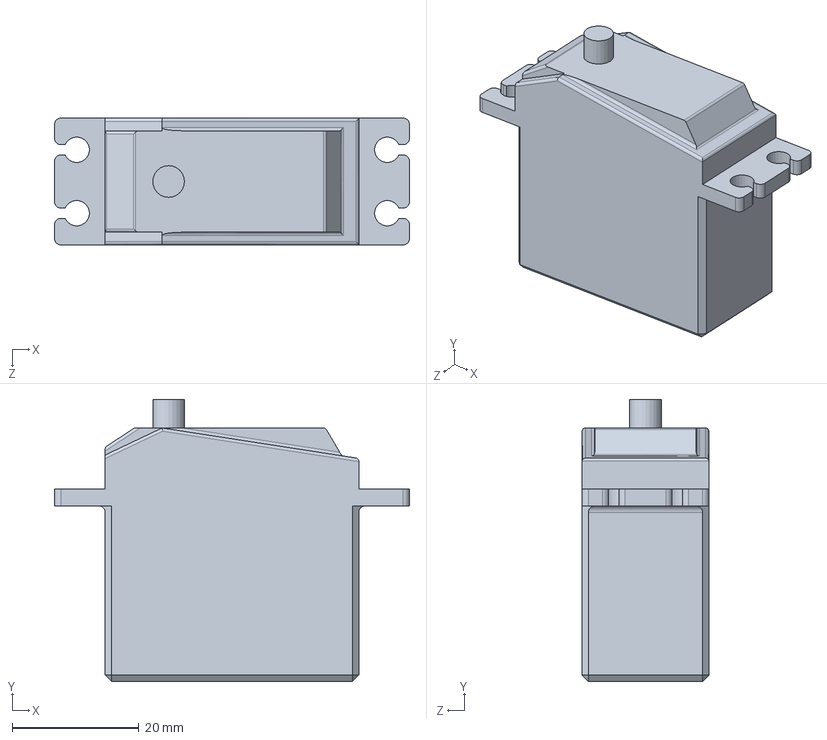
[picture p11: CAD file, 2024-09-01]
model/智能视觉车四分类/舵机1.SLDPRT
56.0 x 44.5 x 20.0 mm

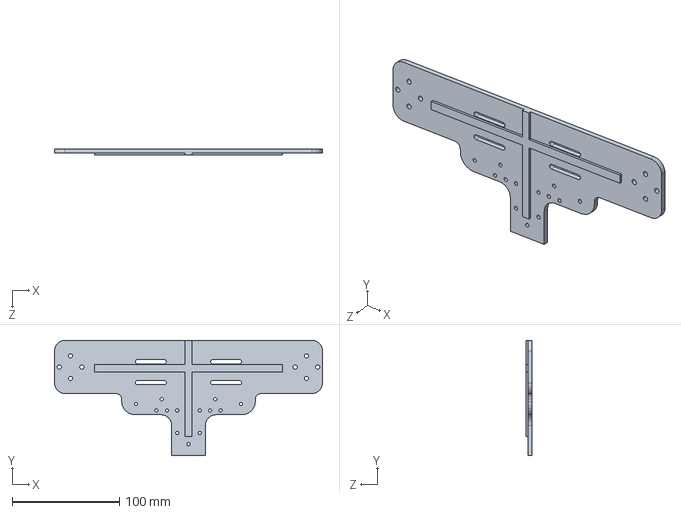
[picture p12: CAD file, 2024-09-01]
model/五分类/后支撑小.SLDPRT
250.0 x 107.7 x 6.00 mm

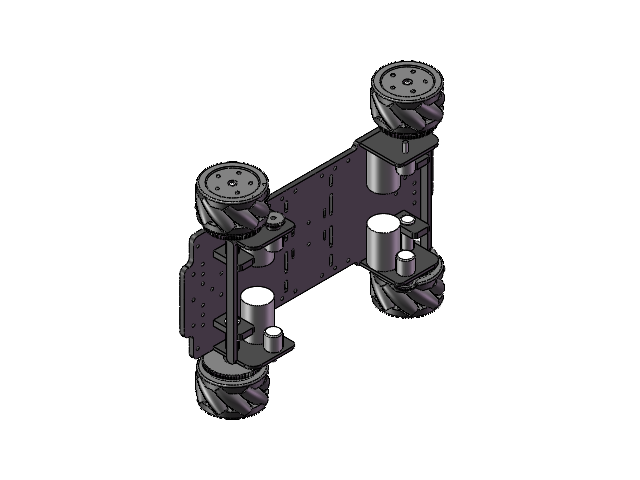
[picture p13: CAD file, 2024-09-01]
model/false佬开源车模/m车模.SLDASM
底板
车轮轴 x 4
麦轮 x 4
编码器齿轮 x 2

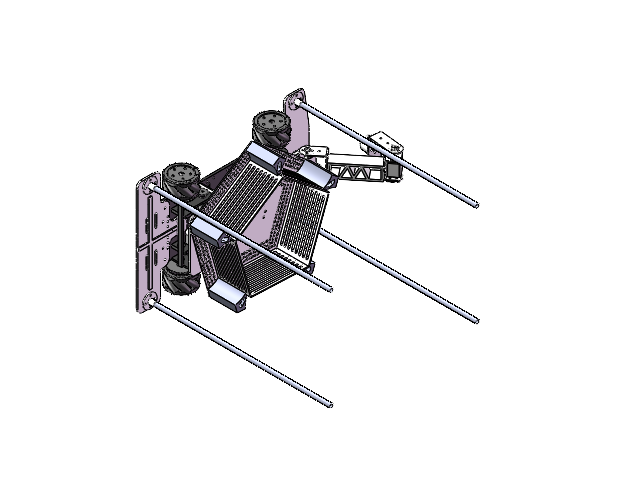
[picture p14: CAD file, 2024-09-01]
model/五分类/m车模.SLDASM
底板
车轮轴 x 4
麦轮 x 4
编码器齿轮 x 2
后支撑小
前支撑小
仓支架
推力轴承
铜柱 x 4
40cm碳杆 x 4
碳杆底座 x 4
零件1
仓挡板 x 5
仓零件 x 5
机械臂连接
舵机1 x 2
长U支架
杯式轴承 x 2
万能支架 x 2
舵盘 x 2
短U支架
电磁铁 x 2

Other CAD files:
model/智能视觉车四分类/智能视觉车1.SLDASM
model/四分类/装配体1.SLDASM
model/智能视觉车四分类/四分类/装配体1.SLDASM
model/五分类/40cm碳杆.SLDPRT
model/四分类/M车底盘.SLDPRT
model/四分类/三脚架.SLDPRT
model/四分类/三角固定.SLDPRT
model/四分类/三通.SLDPRT
model/四分类/仓支架.SLDPRT
model/四分类/前支撑.SLDPRT
model/四分类/加固.SLDPRT
model/四分类/后支撑.SLDPRT
model/四分类/后支撑（单.SLDPRT
model/四分类/机械臂连接.SLDPRT
model/四分类/电磁铁.SLDPRT
model/四分类/电磁铁2.SLDPRT
model/四分类/直角连接.SLDPRT
model/四分类/碳杆.SLDPRT
model/四分类/碳杆2.SLDPRT
model/四分类/碳杆260.SLDPRT
model/四分类/碳杆底座.SLDPRT
model/四分类/舱门.SLDPRT
model/智能视觉车四分类/M车底盘.SLDPRT
model/智能视觉车四分类/pvc三通.SLDPRT
model/智能视觉车四分类/pvc管.SLDPRT
model/智能视觉车四分类/万能支架.SLDPRT
model/智能视觉车四分类/五分类/仓挡板.SLDPRT
model/智能视觉车四分类/五分类/仓支架.SLDPRT
model/智能视觉车四分类/五分类/仓零件.SLDPRT
model/智能视觉车四分类/五分类/固定.SLDPRT
model/智能视觉车四分类/五分类/左舵机支架.SLDPRT
model/智能视觉车四分类/五分类/左舵机支架1.SLDPRT
model/智能视觉车四分类/五分类/零件1.SLDPRT
model/智能视觉车四分类/五分类/零件3.SLDPRT
model/智能视觉车四分类/五分类/零件5.SLDPRT
model/智能视觉车四分类/仓支架.SLDPRT
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

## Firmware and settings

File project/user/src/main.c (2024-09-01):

#include "zf_common_headfile.h"
#include "my_motor.h"
#include "my_servo.h"
#include "my_encoder.h"
#include "my_image.h"
#include "my_key.h"
#include "image.h"
#include "math.h"
#include "imu660ra.h"
#include "car_control.h"
#include "my_buzzer.h"
#include "menu.h"

uint8 data_buffer[32];//测试用
int16 Target_Speed=1; //测试用

void pit_handler_3()
{
	// FW_Data[0].type = 'd';
	// FW_Data[1].type = 'd';
	// FW_Data[2].type = 'd';
	// // FW_Data[2].type = 'f';
	// // FW_Data[3].type = 'd';
	// // FW_Data[4].type = 'd';
	// FW_Data[0].int_data = track_wide;
	// FW_Data[1].int_data = lose_point_num_L;
	// FW_Data[2].int_data = lose_point_num_R;
	// // FW_Data[2].float_data =  imu660ra_gyro_z;
	// // FW_Data[3].int_data =  track_wide;
	// // FW_Data[4].int_data =  Slope;
	// FireWater_Send();

	if(abs(Gyro_Angle.Zdata - angle_now - angle_turn)<5)	//小于3度就认为转向完成
	{
		Image_Mode = 0;
		Control_Mode = 0;
		pit_disable(PIT_CH3);
	}
	else
	{
		Control_Mode = 3;
	}
	// if(CHECK_TIMER_ENABLE)
	// {
	// 	uint32 time = timer_get(GPT_TIM_1);
	// 	if(time>=set_time_ms)
	// 	{
	// 		Image_Mode = 0;
	// 		Control_Mode = 0;
	// 		timer_stop(GPT_TIM_1);
	// 		timer_clear(GPT_TIM_1);
	// 		pit_disable(PIT_CH3);
	// 		CHECK_TIMER_ENABLE = false;
	// 	}
	// }
}

int main(void)
{
	
    clock_init(SYSTEM_CLOCK_600M);  // 不可删除
    debug_init();                   // 调试端口初始化
	system_delay_ms(500);

	//注意！！！屏幕对电机有影响
	//spi_init(SPI_1, 0, 1*1000*1000, SPI1_SCK_D12, SPI1_MOSI_D14, SPI1_MISO_D15, SPI1_CS0_D13);
	//ips200_init(IPS200_TYPE_SPI);
	//(IPS200_CROSSWISE);
	//ips200_init(IPS200_TYPE_PARALLEL8);
	ips114_set_dir(IPS114_CROSSWISE);
	ips114_init();
	key_index_enum key_index_array[KEY_NUMBER] = {KEY_1,KEY_2,KEY_3,KEY_4};
    key_init(5);
    // 此处编写用户代码 例如外设初始化代码等
	my_imu660ra_init();
	imu660_zeroBias();
	my_servo_init();
	
	//my_key_init();
	buzzer_init();
    //wireless_uart_init();
	
	//ImagePerspective_Init();
	my_uart_init();
	//下面三个初始化放在最后，因为含有pit初始化
	
	my_image_init();
	my_motor_init();	//--->>>>>>>>>注意这里的D12-D15引脚与ips200的csi重复使用，不能同时使用
 	my_encoder_init();	//对屏幕显示可能也有影响
	//timer_init(GPT_TIM_1,TIMER_US);
	IR_init();

	timer_init(GPT_TIM_1, TIMER_MS);

 	interrupt_set_priority(LPUART8_IRQn,4);
	interrupt_set_priority(PIT_IRQn, 0);
	interrupt_set_priority(LPUART1_IRQn,1);
	interrupt_set_priority(LPUART4_IRQn,2);
	interrupt_global_enable(0);

	pit_ms_init(PIT_CH0, 3);	//编码器
	pit_ms_init(PIT_CH1, 5);	//陀螺仪
	pit_ms_init(PIT_CH2, 5);	//总钻风
	pit_ms_init(PIT_CH3, 10);	//无线串口发送
	pit_disable(PIT_CH3);
    // 此处编写用户代码 例如外设初始化代码等
												
	ips114_draw_line(middle -  30, 20, middle + 30, 20, RGB565_GREEN);
	ips114_draw_line(0,40,187+40,40,RGB565_PURPLE);
	ips114_draw_line(0,80,187+40,80,RGB565_PURPLE);
	ips114_draw_line(188,20,187+40,20,RGB565_GREEN);
	ips114_draw_line(188,100,187+40,100,RGB565_GREEN);
	while(1)
    {	
		if(mt9v03x_finish_flag)
        {
			mt9v03x_finish_flag = 0;
			//ips114_show_gray_image(0, 0, (const uint8 *)mt9v03x_image, MT9V03X_W, MT9V03X_H, 188, 120, 0);

			// mt9v03x_finish_flag = 0;
			// sideline_correct(boder_correct, &sideline_angle, &sideline_distance);
		
		}
		// ips114_show_uint(90,90,track_wide,4);
		// show_boder_line();
		// //ips114_show_int(188, 70, find_white_point(mt9v03x_image), 3);
		// ips114_show_int(30,10,roundabout_flag, 2);
		// ips114_show_int(30,30,lose_point_num_L, 3);
		// ips114_show_int(30,50,lose_point_num_R, 3);
		// ips114_show_int(30,70,curvity_calculate(boder_L, &longest), 6);
		// ips114_show_int(30,90,curvity_calculate(boder_R, &longest), 4);
		
		//ips114_show_int(50,110,Slope, 2);
		// ips114_show_int(50,40,uart1_data_arr[0], 4);
		// ips114_show_int(90,40,uart1_data_arr[1], 4);
		// system_delay_ms(10);
		

		//Slope_Mode = 2;
		//target_slope  = -30;

		// arm_up_part1();
		//arm_down();
		// arm_exchange(0,1);
		// arm_hang();
		// arm_exchange(1,2);
		// arm_hang();
		// //system_delay_ms(200);
		// arm_exchange(2,3);
		// arm_hang();

		//system_delay_ms(500);
		// arm_exchange(1,2);
		// arm_exchange(2,1);
//		arm_exchange(1,0);

		// arm_up();
		// //system_delay_ms(500);
		// arm_hang();

		start_finish_line_control();
		cross_move_control();
		roundabout_move_control();
		ART_control();
		// ramp_control();
		// barrier_control();	

		system_delay_ms(5);
		key_scanner();
		UI();
		 
		// else if(KEY_LONG_PRESS == key_get_state(KEY_2))
		// {
		// 	ips114_show_string(0,40,"key2");
		// }

		//ips114_show_string(0,120,"test6");
		//arm_down();
		// arm_exchange(0,1);
		//arm_hang();
		//arm_up();
		//arm_hang();
		//curvity_calculate(boder_L,&longest);
//		system_delay_ms(500);
//		arm_exchange(1,0);
//	system_delay_ms(500);
//		
		
    }
}







//------------------------------测试代码------------------------------------

// ips114_show_int(30,30,roundabout_flag, 2);
// ips114_show_int(30,50,track_wide, 5);
// ips114_show_int(30,70,turn_flag, 2);
// ips114_show_int(30,90,cross_flag, 2);
// ips114_show_int(30,110,Control_Mode, 2);



// system_delay_ms(10);
// for(uint8 i = 0; i<=3; i++)
// {
// 	Servo_SetAngle(3,i*93);
// 	system_delay_ms(1500);
// 	arm_down();
// 	arm_hang();
// } 	

// //	JF_Data.data[0] = Kp_T;
// //	JF_Data.data[1] = Kd_T;
// //	JF_Data.data[2] = 0.45;
// //	JF_Data.data[3] = -3.36;
// //	JustFloat_Send();
// FW_Data[0].type = 'd';
// FW_Data[1].type = 'd';
// //FW_Data[2].type = 'd';
// //FW_Data[3].type = 'd';

//  FW_Data[4].type = 'f';
//  FW_Data[5].type = 'f';

// //FW_Data[6].type = 'd';
// //FW_Data[7].type = 'd';

// FW_Data[0].int_data = encoder_data[0];
// FW_Data[1].int_data = encoder_data[1];
// // FW_Data[2].int_data = encoder_data[2];
// // FW_Data[3].int_data = encoder_data[3];

//  FW_Data[4].float_data = Kp_correct2;
//  FW_Data[5].float_data = Kd_correct2;
// // FW_Data[6].int_data = Pwm[0];
// // FW_Data[7].int_data = Pwm[1];
// FireWater_Send();



//定时器测量时间
//			 timer_start(GPT_TIM_1);			 			 
//			 timer_stop(GPT_TIM_1);
//			 uint32 time = timer_get(GPT_TIM_1);
//			 timer_clear(GPT_TIM_1);
//			 ips200_show_int(50, 50, time, 4);


 //逆透视
//			 uint8_t show[RESULT_ROW][RESULT_COL];
//                for(int i=0;i<RESULT_ROW;i++)
//                {
//                    for(int j=0;j<RESULT_COL;j++)
//                    {
//                        show[i][j]=ImageUsed[i][j];
//                    }
//                }
//            ips200_show_gray_image(0,130,show[0],RESULT_COL,RESULT_ROW,RESULT_COL,RESULT_ROW,0);


//		uint8 image_copy[MT9V03X_H][MT9V03X_W];
//		if(mt9v03x_finish_flag)
//		{	zf_assert(NULL != &image_copy[0][0]);
//			mt9v03x_finish_flag = 0;
//		
//			memcpy(image_copy[0], mt9v03x_image[0], MT9V03X_IMAGE_SIZE);
//			wireless_uart_send_buffer((const uint8*)preFrame, sizeof(int)*7);
//			wireless_uart_send_buffer(&image_copy[0][0], MT9V03X_IMAGE_SIZE);
//		}


//uint8 data_len = wireless_uart_read_buffer(data_buffer, 32);  
// 		if(data_len != 0)                                                       // 收到了消息 读取函数会返回实际读取到的数据个数
//         {
//			 //printf(data_buffer);
//             wireless_uart_send_buffer(data_buffer, data_len);                     // 将收到的消息发送回去
//             //memset(data_buffer, 0, 32);
//// 			sscanf((const char*)data_buffer, "@:%d,%d",&v_x, &v_y);
//// 			memset(data_buffer, 0, 32);
//         }
		//printf("%d,%d, %d\n",v_x, v_y, w);


// if(packge_finish_flag)
		// 	//printf("data:%d,%d,%c\n", data_arr[0], data_arr[1], data_arr[2]);
		// 	ips200_show_int(20,20,data_arr[0],3);
		// 	ips200_show_int(20,40,data_arr[1],3);
			//packge_finish_flag = 0;



		// v_y = 0;
		// v_x =0;
		// system_delay_ms(2000);
		// v_y = -90;//0;
		// v_x =0;//-30;
		// system_delay_ms(2000);
//		v_y = -30;
//		v_x =0;
//		system_delay_ms(1000);
//		v_y = 0;
//		v_x =30;
//		system_delay_ms(1000);

//system_delay_ms(1500);
		//system_delay_ms(1000);
		//		Target_Speed = 35;
		//		system_delay_ms(4000);
		// 		Target_Speed = -35;
		// 		system_delay_ms(4000);


//my_key_work();
		//ips114_show_float(100,100,Kp_T, 2,1);
		// ips114_show_float(0,20,Kp_correct1, 3,3);
		// ips114_show_float(0,40,Kd_correct1, 3,3);
//------------------------------测试代码------------------------------------

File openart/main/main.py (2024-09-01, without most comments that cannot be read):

# Untitled - By: 86152 - Wed Jun 5 2024

import seekfree, pyb
import sensor, image, time, math
import os, tf,gc
from machine import UART

lcd = seekfree.LCD180(2)
lcd.full()

uart = UART(2, baudrate=115200)

sensor.reset()
sensor.set_pixformat(sensor.RGB565)
sensor.set_framesize(sensor.QVGA)   # 设置摄像头分辨率
sensor.set_brightness(700)
sensor.skip_frames(time = 200)
clock = time.clock()


#设置模型路径
face_detect ='/sd/yolo3_iou_smartcar_final_with_post_processing1.tflite'
#载入模型
net = tf.load(face_detect)


net_path_a = "mobilenet_a.tflite"
labels = [line.rstrip() for line in open("/sd/labels.txt")]   # 加载标签
net2 = tf.load(net_path_a, load_to_fb=True)                                  # 加载模型

net_path_d = "mobilenet_d.tflite"
labels_d = [line.rstrip() for line in open("/sd/labels_d.txt")]   # 加载标签
net3 = tf.load(net_path_d, load_to_fb=True)                                  # 加载模型


label_map = {
    0: "object"
   }


find_card = 0
sorted_list= []
uart_data= '0'
brightness=700

card_class_record = [0,0,0,0,0]   # 前五次记录的卡片类别

def uart_classify(img):
    global find_card,sorted_list,uart_data
    if uart_data=='0':
        img0 = img.copy(x_size=240,y_size=240)
        for obj in tf.detect(net,img0):
            x1,y1,x2,y2,label,scores = obj
            if(scores>0.70):
                find_card += 1
                #print(obj)
                w = x2- x1
                h = y2 - y1
                x1 = int((x1)*img.width())
                y1 = int(y1*img.height())
                w = int(w*img.width())
                h = int(h*img.height())
                if x1<0:
                    x1=0
                if y1<0:
                    y1=0
                img.draw_rectangle((x1,y1,w,h),thickness=2)
                label_name = label_map.get(label, "未知类别")
                img1 = img.copy(roi = (x1,y1,w,h),copy_to_fb=False)
                for obj1 in tf.classify(net2, img1, min_scale=1.0, scale_mul=0.5, x_overlap=0.0, y_overlap=0.0):
                    sorted_list = sorted(zip(labels, obj1.output()), key = lambda x: x[1], reverse = True)
    elif uart_data=='1':
        for r in img.find_rects(threshold = 40000):             # 在图像中搜索矩形
            s = r.w()*r.h()
            #print("S:%d"%s)
            if(s > 20000 or s < 5000):
                continue

            find_card += 1
            img.draw_rectangle(r.rect(), color = (255, 0, 0))   # 绘制矩形外框，便于在IDE上查看识别到的矩形位置
            img1 = img.copy(1, 1, r.rect())                           # 拷贝矩形框内的图像
            for obj1 in tf.classify(net3, img1, min_scale=1.0, scale_mul=0.5, x_overlap=0.0, y_overlap=0.0):
                sorted_list = sorted(zip(labels_d, obj1.output()), key = lambda x: x[1], reverse = True)

# 前几次类别记录
def class_record(card_class):
    global card_class_record

    #将传入的最新卡片类别更新到前五次类别记录列表中
    for i in range(2):
        card_class_record[i] = card_class_record[i+1]

    card_class_record[2] = card_class

    # 判断前五次类别是否相同
    if all(card_class == each_class for each_class in card_class_record[:3]):
#        print('okokokok')
        return True
    else:
#        print('nononono')
        return False


while(True):
    while uart.any():
       uart_data = uart.read(1).decode() # 读取串口数据

    if uart_data =='a':
        brightness+=50
        uart_data='0'
    elif uart_data =='b':
        brightness-=50
        uart_data='0'
    sensor.set_brightness(brightness)

    find_card = 0

    img = sensor.snapshot()
    uart_classify(img)
    lcd.show_image(img, 320, 240, zoom=2)
    # 更新记录列表并判断与前4次是否相等
    if sorted_list:
        if((find_card>0) and class_record(sorted_list[0][0])):
            uart.write("Y%s,1Z" %(sorted_list[0][0]))
            lcd.show_str(sorted_list[0][0],0, 44, lcd.RED, 1)
            #print("Y%s,1Z,%s" %(sorted_list[0][0],uart_data))
        else:
            uart.write("Y0,0Z")
            lcd.show_str(sorted_list[0][0],0, 44, lcd.RED, 1)
            #lcd.show_str("0",0, 44, lcd.RED, 1)
           # print("Y%s,0Z,%s" %(sorted_list[0][0],uart_data))
        #lcd.show_image(img, 320, 240, zoom=2)
        #lcd.show_str(sorted_list[0][0],0, 44, lcd.RED, 1)
    #sorted_list= []
    #sorted_list[0] = ("0", sorted_list[0][1])
    lcd.show_str(uart_data,0, 0, lcd.RED, 1)
    lcd.show_str(str(brightness),0, 60, lcd.RED, 1)
    gc.collect()



if __name__ == '__main__':
    main()

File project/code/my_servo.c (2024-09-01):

#include "zf_common_headfile.h"

#define SERVO_MOTOR_PWM1             (PWM4_MODULE2_CHA_C30)  //机械臂舵机1                     // 定义主板上舵机对应引脚
#define SERVO_MOTOR_PWM2             (PWM2_MODULE1_CHA_C8)   //机械臂舵机2
#define SERVO_MOTOR_PWM3             (PWM2_MODULE0_CHB_C7)   //储物舱舵机
#define magnet_PWM             		  (PWM1_MODULE3_CHA_B10)  //PWM2_MODULE3_CHA_B9 //(PWM1_MODULE3_CHA_B10)  //电磁铁


#define SERVO_MOTOR_FREQ            (150)                   // 定义主板上舵机频率  请务必注意范围 50-300
#define SERVO_MOTOR_MaxRange1       (360)   //180               //180度舵机
#define SERVO_MOTOR_MaxRange2       (360)                   //360度舵机  (储物舱的舵机)
#define SERVO_MOTOR_MaxRange3       (360)                   //360度舵机(可控制角度)  (机械臂上面的舵机)

#if (SERVO_MOTOR_FREQ<50 || SERVO_MOTOR_FREQ>330)
    #error "SERVO_MOTOR_FREQ ERROE!"
#endif
// ------------------ 舵机占空比计算方式 ------------------
// 
// 舵机对应的 0-180 活动角度对应 控制脉冲的 0.5ms-2.5ms 高电平
// 
// 那么不同频率下的占空比计算方式就是
// PWM_DUTY_MAX/(1000/freq)*(0.5+Angle*2/180) 在 50hz 时就是 PWM_DUTY_MAX/(1000/50)*(0.5+Angle*2/180)
// 
// 那么 100hz 下 90度的打角 即高电平时间1.5ms 计算套用为
// PWM_DUTY_MAX/(1000/100)*(1+90*2/SERVO_MOTOR_MaxRange) = PWM_DUTY_MAX/10*1.5
// 
// ------------------ 舵机占空比计算方式 ------------------
#define Arm_Servo1_Angle(x)         ((float)PWM_DUTY_MAX/(1000.0/(float)SERVO_MOTOR_FREQ)*(0.5+(float)(x)*2/SERVO_MOTOR_MaxRange1))
#define Arm_Servo2_Angle(x)         ((float)PWM_DUTY_MAX/(1000.0/(float)SERVO_MOTOR_FREQ)*(0.5+(float)(x)*2/SERVO_MOTOR_MaxRange3))
#define Box_Servo_Angle(x)         ((float)PWM_DUTY_MAX/(1000.0/(float)SERVO_MOTOR_FREQ)*(0.5+(float)(x)*2/SERVO_MOTOR_MaxRange2))

#define BOX_OFFSET	83
#define ARM1_OFFSET	-165
#define ARM2_OFFSET	3
#define SERVO_SPEED	1		//舵机打角速度，0为正常模式，1为slow模式
#define is_IR   true        //是否开启IR来检测卡片拾取是否到位

//用于在Servo_SetAngle_Slow里记录角度	
static uint32 current_angle[3] = {100, 80, 0};    //初始化为主板上电后各个舵机的角度，对应pwm初始设置的参数

void my_servo_init(void)
{  
    pwm_init(SERVO_MOTOR_PWM1, SERVO_MOTOR_FREQ, (uint32)Arm_Servo1_Angle(360-95+ARM1_OFFSET)); //100
    pwm_init(SERVO_MOTOR_PWM2, SERVO_MOTOR_FREQ, (uint32)Arm_Servo1_Angle(80+ARM2_OFFSET));
    system_delay_ms(200);
    pwm_init(SERVO_MOTOR_PWM3, SERVO_MOTOR_FREQ, (uint32)Box_Servo_Angle(0+BOX_OFFSET));
	
	//电磁铁初始化
	pwm_init(magnet_PWM, 10000, 0);

    //pwm_init(PWM2_MODULE3_CHA_B9, 1000, 9000);
    gpio_init(B9, GPO, 1, GPO_PUSH_PULL);
	current_angle[0] = 360-95+ARM1_OFFSET;
	current_angle[1] = 80+ARM2_OFFSET;
	current_angle[2] = 0+BOX_OFFSET;
	
}

//电磁铁， state:0关闭， 1开启
uint8 magnet_scale = 1; //吸力强度：1吸力一般，2吸力较强
void magnet_set(uint8 state)
{
	if(state == 0){ pwm_set_duty(magnet_PWM, 0); }
	else if(state == 1)
    {
        if(magnet_scale == 1)pwm_set_duty(magnet_PWM, 7142);//7142
        else if(magnet_scale == 2)pwm_set_duty(magnet_PWM, 10000);
        
    }
}

void Servo_SetAngle( uint8 servo_num, uint32 angle )
{
    current_angle[servo_num-1] = angle;   //更新当前角度
    switch (servo_num)
    {
        case 1:
            pwm_set_duty(SERVO_MOTOR_PWM1,(uint32)Arm_Servo1_Angle(360-angle+ARM1_OFFSET));
			current_angle[0] = 360-angle+ARM1_OFFSET;
            // system_delay_ms(50);
            // pwm_set_duty(SERVO_MOTOR_PWM1,0);
            break;
        case 2:
            pwm_set_duty(SERVO_MOTOR_PWM2,(uint32)Arm_Servo2_Angle(angle+ARM2_OFFSET));
            // system_delay_ms(50);
            // pwm_set_duty(SERVO_MOTOR_PWM2,0);
            current_angle[1] = angle+ARM2_OFFSET;
            break;
        case 3:
            pwm_set_duty(SERVO_MOTOR_PWM3,(uint32)Box_Servo_Angle(angle+BOX_OFFSET));
            // system_delay_ms(50);
            // pwm_set_duty(SERVO_MOTOR_PWM3,0);
            current_angle[2] = angle+BOX_OFFSET;   //更新记录的当前角度,不要忘了有偏移角度
            break;
        default:
            break;
    }
}

//-----------------------------------------------------------------------------------------------
// 函数简介  设置舵机角度（有延时，转得慢）
// 参数说明  servo_num：舵机编号， angle：要设置的角度
// 返回参数  void
// 使用示例  
// 备注信息  若在my_servo_init里初始化pwm时改了初始设置的角度，则这里也应更改静态数组current_angle的初始值
//-----------------------------------------------------------------------------------------------
void Servo_SetAngle_Slow(uint8 servo_num, uint32 angle)
{
    if(servo_num == 3)
    {
        angle += BOX_OFFSET;
    }
	if(servo_num == 1)
    {
        angle = 360-angle+ARM1_OFFSET;
    }
    if(servo_num == 2)
    {
        angle = angle+ARM2_OFFSET;
    }
    while(current_angle[servo_num-1]!=angle)
    {
        if     (current_angle[servo_num-1]<angle)current_angle[servo_num-1]+=1;
        else if(current_angle[servo_num-1]>angle)current_angle[servo_num-1]-=1;

        switch (servo_num)
        {
            case 1:
                pwm_set_duty(SERVO_MOTOR_PWM1,(uint32)Arm_Servo1_Angle(current_angle[servo_num-1]));
				system_delay_ms(4);
                break;
            case 2:
                pwm_set_duty(SERVO_MOTOR_PWM2,(uint32)Arm_Servo2_Angle(current_angle[servo_num-1]));
				system_delay_us(2000);
                break;
            case 3:
                pwm_set_duty(SERVO_MOTOR_PWM3,(uint32)Box_Servo_Angle(current_angle[servo_num-1]));
                system_delay_ms(3);
            default:
                break;
        }
        //system_delay_ms(5);       //设置的延时时间
    }
}   

bool arm_down()
{
    bool state;

#if SERVO_SPEED == 1
	
    Servo_SetAngle(2, 29);
    system_delay_ms(200+100);
    Servo_SetAngle(1, 100);
    system_delay_ms(150+100); 
    Servo_SetAngle(1, 78);
	magnet_set(1); 
    system_delay_ms(250);   
	Servo_SetAngle(1, 90);
	system_delay_ms(50);
	Servo_SetAngle(1, 95);
	Servo_SetAngle(2, 35);
	system_delay_ms(50);
    Servo_SetAngle(1, 100);
	Servo_SetAngle(2, 40);
    system_delay_ms(50);
    Servo_SetAngle(2, 240);
    system_delay_ms(300);
    if(IR_get_state() == 0)
    {
        state = true;
        buzzer_set_delay(100);
    }
    else
    {
        state = false;
    }
    Servo_SetAngle(1, 130);
    system_delay_ms(300);
    magnet_set(0);
	
#elif SERVO_SPEED == 0
   
	Servo_SetAngle_Slow(2, 29);
    Servo_SetAngle_Slow(1, 80);
	magnet_set(1); 
    system_delay_ms(100);
	Servo_SetAngle_Slow(1, 95);
	Servo_SetAngle_Slow(2, 35);
    Servo_SetAngle_Slow(2, 240);
    if(IR_get_state() == 0)
    {
        state = true;
        buzzer_set_delay(100);
    }
    else
    {
        state = false;
    }
    Servo_SetAngle_Slow(1, 150);
    magnet_set(0);

#endif

    return state;
}

//返回值:是否拾取上来，false-没有拾取上来，true-成功拾取上来
bool arm_up()
{
    bool state;     //记录本次拾取是否成功
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

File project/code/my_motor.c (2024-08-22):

#include "zf_common_headfile.h"
#include "my_motor.h"
#include "imu660ra.h"
#include "my_image.h"
#include <math.h>


#define r_x                 0.089//8.9 //左右两轮轴间距的一半(cm)
#define r_y                  0.1//10  //前后两轮轴间距的一半(cm)

uint32 set_time_ms = 0; //设定的计时器时间
bool CHECK_TIMER_ENABLE = false;    //检查计时器计数值是否使能neg
bool SPEED_ENABLE = false;  //速度使能,默认关闭，故刚启动时需要手动按键才会使能运动
float angle_now = 0;    //进入环岛十字时的角度
float angle_turn = 0;   //需要转的角度
float target_angle = 0; //设定的角度值
float target_slope  = 0;  //目标斜率
int16 tracking_speed = 40;//60;  //循迹速度
int16 last_speed_y = 40;    //上次的v_y
int16 speed_offset = 10;    //速度偏移量
uint8 Control_Mode = 0;     //0-正常循迹， 1-边界矫正,2卡片矫正模式,3陀螺仪转向，4等待模式， 5赛道两边的边界矫正，6角度闭环模式
uint8 Correct_Mode = 0;     //卡片矫正模式，0-拾取卡片矫正，1-放卡片矫正
uint8 turn_flag = 0;    //转向完成标志位（用于环岛十字的转向）

float Inc_Kp[4]={45, 45, 45, 45};//10//6.5/100
float Inc_Ki[4]={5.5, 5.5, 5.5, 5.5};//0/64/4.8
float Inc_Kd[4]={0, 0, 0, 0};//1.1
int16 v_w[4]={0};       //四个轮子的转速
int16 v_x = 0, v_y = 40, w = 0;  //x、 y轴分速度,车绕几何中心的角速度
int16 Pwm[4]={0};
int16 bias;
int16 motor_bias_last[4];
int16 motor_bias_last2[4];

void my_motor_init()
{
    gpio_init(MOTOR1_DIR, GPO, GPIO_HIGH, GPO_PUSH_PULL);                            // GPIO 初始化为输出 默认上拉输出高
    pwm_init(MOTOR1_PWM, 17000, 0);                                                  // PWM 通道初始化频率 17KHz 占空比初始为 0
    
    gpio_init(MOTOR2_DIR, GPO, GPIO_HIGH, GPO_PUSH_PULL);                            // GPIO 初始化为输出 默认上拉输出高
    pwm_init(MOTOR2_PWM, 17000, 0);                                                  // PWM 通道初始化频率 17KHz 占空比初始为 0

    gpio_init(MOTOR3_DIR, GPO, GPIO_HIGH, GPO_PUSH_PULL);                            // GPIO 初始化为输出 默认上拉输出高
    pwm_init(MOTOR3_PWM, 17000, 0);                                                  // PWM 通道初始化频率 17KHz 占空比初始为 0

    gpio_init(MOTOR4_DIR, GPO, GPIO_HIGH, GPO_PUSH_PULL);                            // GPIO 初始化为输出 默认上拉输出高
    pwm_init(MOTOR4_PWM, 17000, 0); 
}

void motor_set_duty(uint8 motor_num, int16 duty)
{
	//ips114_show_int(40,40,duty,5);
	duty = func_limit(duty, 8000);
    if(duty >= 0)   //正转
    {
        if(motor_num == 1) { gpio_set_level(MOTOR1_DIR, GPIO_HIGH); pwm_set_duty(MOTOR1_PWM, (uint32_t)duty);}
        if(motor_num == 2) { gpio_set_level(MOTOR2_DIR, GPIO_HIGH); pwm_set_duty(MOTOR2_PWM, (uint32_t)duty);}

        if(motor_num == 3) { gpio_set_level(MOTOR3_DIR, GPIO_LOW); pwm_set_duty(MOTOR3_PWM, (uint32_t)duty);} //gpio_set_level(MOTOR3_DIR, GPIO_LOW); pwm_set_duty(MOTOR3_PWM, (uint32_t)duty);
        if(motor_num == 4) { gpio_set_level(MOTOR4_DIR, GPIO_LOW); pwm_set_duty(MOTOR4_PWM, (uint32_t)duty);} //gpio_set_level(MOTOR4_DIR, GPIO_LOW); pwm_set_duty(MOTOR4_PWM, (uint32_t)duty);
    }
    else           //反转
    {
        if(motor_num == 1) { gpio_set_level(MOTOR1_DIR, GPIO_LOW); pwm_set_duty(MOTOR1_PWM, (uint32_t)-duty);}
        if(motor_num == 2) { gpio_set_level(MOTOR2_DIR, GPIO_LOW); pwm_set_duty(MOTOR2_PWM, (uint32_t)-duty);}

        if(motor_num == 3) { gpio_set_level(MOTOR3_DIR, GPIO_HIGH); pwm_set_duty(MOTOR3_PWM, (uint32_t)-duty);}//gpio_set_level(MOTOR3_DIR, GPIO_HIGH); pwm_set_duty(MOTOR3_PWM, (uint32_t)abs_duty);
        if(motor_num == 4) { gpio_set_level(MOTOR4_DIR, GPIO_HIGH); pwm_set_duty(MOTOR4_PWM, (uint32_t)-duty);}//gpio_set_level(MOTOR4_DIR, GPIO_HIGH); pwm_set_duty(MOTOR4_PWM, (uint32_t)abs_duty);
    }   
}

//增量式PI速度环
int16 Incremental_PI (uint8 motor_num, int16 Encoder, int16 Target)
{ 		
    int16 bias = Target - Encoder ;
	Pwm[motor_num-1] += ( Inc_Kp[motor_num-1]*(bias-motor_bias_last[motor_num-1]) 
                        + Inc_Ki[motor_num-1]*bias
                        + Inc_Kd[motor_num-1]*(bias-2*motor_bias_last[motor_num-1] + motor_bias_last2[motor_num-1] ));
    motor_bias_last2[motor_num-1] = motor_bias_last[motor_num-1];
    motor_bias_last[motor_num-1] = bias;
    
    //积分限幅
    if(Pwm[motor_num-1]> 8000)Pwm[motor_num-1]= 8000;
    if(Pwm[motor_num-1]<-8000)Pwm[motor_num-1]=-8000;
	
    return (int16)Pwm[motor_num-1];
}

//-----------------------------------------------------------------------------------------------
// 函数简介  麦克纳姆轮解算
// 参数说明  v_x: x方向的速度
// 参数说明  v_y: y方向的速度
// 参数说明  w:   车身角速度
// 返回参数  void
// 使用示例  
// 备注信息  将v_x, v_y,w这三个参数传入即可解算出四个轮子的转速
//-----------------------------------------------------------------------------------------------		                                  
void car_omni(int16 v_x, int16 v_y, int16 w)
{
    v_w[0] = v_y - v_x + w*(r_x + r_y);
    v_w[1] = v_y + v_x - w*(r_x + r_y);
    v_w[2] = v_y - v_x - w*(r_x + r_y);
    v_w[3] = v_y + v_x + w*(r_x + r_y);
}

void Turn_Left()
{
    v_x = 0;
    v_y = 0;
    w = 20;
	car_omni(v_x, v_y, w);
}

//-----------------------------------------------------------------------------------------------
// 函数简介  循迹转向函数
// 参数说明  Target_slope：目标斜率
// 参数说明  actual_slope：实际斜率
// 返回参数  void
// 使用示例  
// 备注信息  通过总钻风计算的斜率传入此函数来计算转向值，从而循迹
//-----------------------------------------------------------------------------------------------
float Kp_T=2.5, Kd_T=15; //2.6， 1.5
void Turn(float Target_slope, float actual_slope)
{
	static float err, err_last;
	err = Target_slope - actual_slope;
    w = Kp_T*err + Kd_T*(err - err_last);
	err_last = err;
	car_omni(v_x, v_y, w);
}
void forward()
{
	v_x = 0;
    v_y = 20;
    w = 0;
	car_omni(v_x, v_y, w);
}
void backward()
{
	v_x = 0;
    v_y = -20;
    w = 0;
	car_omni(v_x, v_y, w);
}
void move(int16 angle, int8 speed)
{
    v_x = speed*cos(angle*3.14/180);
    v_y = speed*sin(angle*3.14/180);
    w = 0;
}

//-----------------------------------------------------------------------------------------------
// 函数简介  到环岛和十字时的横向移动
// 参数说明  sideline_angle:边线倾角误差
// 参数说明  sideline_distance:边线距离误差
// 返回参数  void
// 使用示例  roundabout_move(&sideline_angle, &sideline_distance);
// 备注信息  注意参数为存放数据变量的地址，在调用时传入在my_iamge.c中的全局变量int16 sideline_angle,sideline_distance的地址即可
//-----------------------------------------------------------------------------------------------
float Kp_correct1=1.0, Kd_correct1=10; //0.5 0.2 //1 10
float Kp_correct2=0.12, Kd_correct2=0.4;    //Kp = 0.07 kd = 0.4
static int16 out1, out2;
int16 target_y = 430;   //边线距离矫正的目标值
void roundabout_move(int16* sideline_angle,  int16* sideline_distance)
{

    //使用两个并级PID，第一个：车身倾斜角度修正， 第二个：车身与正前方赛道边界距离修正
    static int16 err1=0, err_last1=0, err2 = 0, err_last2=0;
    
    //车身倾角矫正pid
    err1 = *sideline_angle;
    out1 =Kp_correct1*err1 + Kd_correct1*(err1-err_last1);
	err_last1 = err1;
    out1 = func_limit(out1, 200); //限幅

    //赛道边线距离矫正pid
    err2 = (target_y-*sideline_distance); //目标距离为500个像素点（使用了多个点之和）//450 400   430
    out2 =Kp_correct2*err2 + Kd_correct2*(err2-err_last2);
    err_last2 = err2;
    out2 = func_limit(out2, 400); //限幅

}
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

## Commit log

2024-03-06 Initial commit, can trach the way by grayscale camera
    [RT1064核心板丝印与芯片引脚对应表格.xlsx]
2024-03-23 the pwm has a bug that maybe break out
    pwm值可能会溢出，程序卡死
    [main.c, my_moter.c, my_moter.h]
2024-03-23 corrected the pwm_bug and add vofa files to be more convenient
    pwm bug因该是把无线串口中断的优先级设置为最高的原因，这样可能造成程序卡死
    增加了vofa.c和vofa.h文件，把基本的FireWater和JustFloat引擎封装完善
    但是FireWater发送数据时，第一个通道的数据偶尔会失真，比如要发送的是64，实际子发送了各位4
    [main.c, my_moter.c, vofa.c]
2024-04-09 Update main.c
    你好
2024-04-10 find back the previous code(servo.c/key.c) which was deleted uncautiously
2024-04-11 adjust the angle of arm
2024-04-24 solved problem: uart don't work when using dap
    [main.c, my_uart.c]
2024-05-05 add the change of servo.c
2024-05-28 change the cross and roundabout, but,may be stuck
    [car_control.c, isr.c, main.c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]
2024-06-02 Finish!!! (But some bug with the start_finish_line_control)
    [car_control.c, main.c, my_moter.c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]
2024-06-04 solved bug: runing ouf track when card_correct ; add the judge before turn back when card correct finish
    [car_control.c, main.c, my_moter.c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]
2024-06-04 solved the problem about openart classify add added the dynamic velocity
    [car_control.c, my_moter.c]
2024-06-12 optimized the cross_control and deleted the rt-thread folder also changed the position_correct of "while"
2024-06-18 solved the roundabout bug and velocity slide bug
    [car_control.c, main.c, my_moter.c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]
2024-06-28 add the isSame function and slove other bug but some new bug with releaseing card when there are't rectangle
    [car_control.c, main.c, my_servo.c]
2024-06-29 optimize the servo control add slow mode to avoid to use the delay
    [car_control.c, main.c, my_servo.c]
2024-07-04 add the sideline variance judge to strengthen the barrier and roundabout control add add two ref_point to calculate the distance
    [car_control.c, main.c, main.cpp]
2024-07-07 solve the bug of MCX uart send(&&card_mistake_cnt == 0); add IR to get the state of card_pinking adjust the arm_exchange to be more safer add the slope_mode add the gyro with the barrier control
    [car_control.c, main.c, my_moter.c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]
2024-08-09 add the meau to adjust the para ;change the arm servo1 to 360°
2024-08-10 replace start_finish_line control turn with translation
    [car_control.c, meau.c, my_moter.c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]
